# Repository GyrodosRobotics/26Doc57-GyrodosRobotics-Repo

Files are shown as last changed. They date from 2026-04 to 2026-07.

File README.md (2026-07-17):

<p align="center">
  <img src="https://github.com/GyrodosRobotics/26Doc57-GyrodosRobotics-Repo/raw/9fe3f917eb2502e8cde8e8454340d48af9c0934f/docs/gyrodos-fulllogo.png" alt="Gyrodos Robotics Logo" width=300"/>
</p>

<h1 align="center">Gyrodos Robotics</h1>
<h3 align="center">La Salle College, Hong Kong • Est. 2024</h3>

<p align="center">
  <a href="https://sites.google.com/view/gyrodosrobotics">
    
  </a>
  <a href="https://www.instagram.com/gyrodosrobotics">
    
  </a>
  
  
</p>

---

## About

Gyrodos Robotics is a Hong Kong-based underwater robotics team 
from La Salle College, competing in the MATE ROV Competition. 
Formed in 2024, we are composed of 24 members from Year 7 to 
Year 11 devoted to developing innovative solutions to ocean 
preservation challenges and contributing to the UN Sustainable 
Development Goals 13 and 14.

This repository contains the complete technical output of our 
2026 competition season, including mechanical designs, software systems, 
documentation and internal records that are released openly to support 
the underwater robotics community.

---

## Our Vehicles

### ROV Palkia (26Mec34)
Second-generation Gyrodos flagship ROV. CNC-machined 6061T5 
aluminium frame, dual two-axis Dragon Claw grippers, 
8-camera Compound Eye array with stereo vision and YOLOv11 
invasive species detection, fully_vectored8 thruster layout 
with pseudo-inverse mixing matrix, and the LUCARIO software 
stack over RS422.

### Float Magikarp (26Mag42)
Vertical Profiling Float for below-ice environment monitoring. 
500cc syringe buoyancy engine, PID depth control, Bluetooth 
data transmission, and magnetic reed switch power system.
Built in one month alongside Palkia.

---

## Highlighted Systems

### LUCARIO (267X)
**Logistical Underwater Control and Relay Interface Operator**

Our primary software stack for ROV command, control and monitoring.
Split into independent Core and GUI processes communicating over ZMQ,
with RS422 serial connection to the Arduino Mega at 115200 baud.
Features a precomputed 6×8 pseudo-inverse thruster mixing matrix 
for full 6-DOF control, PID autostabilisation, and the False Swipe 
power management system.

→ [View LUCARIO Code](https://github.com/GyrodosRobotics/26Doc57-GyrodosRobotics-Repo/tree/main/Gyrodos%20G2.2/267X-LUCARIO)

### Dragon Claw (263X)
Dual two-axis gripper system with left and right claws using 
different drive modes to imitate arm and wrist movement. 
60kg IP68 waterproof servo and NEMA 17 stepper with worm gear 
adaptor. Compatible with the Grass Grip friction booster.

→ [View CAD Files](https://github.com/GyrodosRobotics/26Doc57-GyrodosRobotics-Repo/tree/main/Gyrodos%20G2.2/223X-Gyrodos%20ROV/26Mec34-Palkia)

### Grass Grip (223X)
Passive biomimetic extension that distributes clamping force across 
hundreds of contact points for improved grip on irregular objects.
Inspired by 3D printed grass and the principles behind SpiRob 
soft robotics research. Clips onto Dragon Claw in 15 seconds 
without tools.

→ [View STL Files](https://github.com/GyrodosRobotics/26Doc57-GyrodosRobotics-Repo/tree/main/Gyrodos%20G2.2/223X-Gyrodos%20ROV/26Mec34-Palkia)

### Crab Detection (261X)
YOLOv11 model trained on 419 annotated images to identify 
invasive European Green Crab against native Rock and Jonah Crab 
species. mAP50 of 97.4%. Includes undistortion pipeline for 
wide-angle AHD cameras.

→ [View Dedicated Repository](https://github.com/GyrodosRobotics/gyrodos-crab-detection)

---

## Competition Results

| Year | Competition | Result |
|---|---|---|
| 2025 | MATE ROV Ranger Hong Kong Regional | 9th |
| 2026 | MATE ROV Ranger Hong Kong Regional | 6th |
| 2026 | MATE ROV Ranger Hong Kong Regional | Best Team Spirit |
| 2026 | MATE ROV Scout Hong Kong Regional | 2nd |

---

## Documentation

All documents submitted to the 2026 MATE ROV Competition 
are available in `265X-Documentation/`:

- **Technical Documentation** — 25-page full system description
- **Company Spec Sheet** — vehicle specifications
- **JSEA** — Job Safety and Environmental Analysis
- **SID** — System Integration Diagrams for ROV and Float
- **Float Magikarp Specs** — vertical profiling float documentation
- **Company Safety Review** — pre-competition safety verification

---

## Open Source Contributions

| Repository | Description |
|---|---|
| [gyrodos-crab-detection](https://github.com/GyrodosRobotics/gyrodos-crab-detection) | YOLOv11 invasive crab detection model and dataset |
| [This repository](https://github.com/GyrodosRobotics/26Doc57-GyrodosRobotics-Repo) | Complete 2026 season mechanical, software and documentation files |

---

## Team

**C-Suite:**
Keanu Lam (CEO) · Gordon Peng (CTO) · Yiming Huang (COO) · 
Jason Lo (CIO) · David Wang (CQO) · Nixon Li (CMO) · 
Mitchell Au (HR) · Henry Lau (Club Chairman)

**Mentors:** Rex · Jimmy · Cloof · Max

**Teacher Advisor:** Mr Terry Lam · Mr Gary Ho · Mr Timothy Goh · Mr Jonathan Sze

**Full team roster:** See Technical Documentation p.4

---

## Acknowledgements

- Leaplight Limited — CNC machining of aluminium frame
- Makerholic Limited — 3D printing services
- Sparks Solutions — Arduino and relay components
- Autodesk Inc. — Fusion 360 Student licence
- La Salle College — laser cutting equipment and pool access
- MATE Center, MATE II and IET Hong Kong — organising the 
  2026 Hong Kong Regional

---

## Licence

Code: [MIT Licence](LICENSE)  
Dataset and model weights: [CC BY 4.0](https://creativecommons.org/licenses/by/4.0/)  
Documentation: All rights reserved, Gyrodos Robotics 2026

---

<p align="center">
  <em>Gyrodos Robotics • La Salle College • Hong Kong • Est. 2024</em>
</p>

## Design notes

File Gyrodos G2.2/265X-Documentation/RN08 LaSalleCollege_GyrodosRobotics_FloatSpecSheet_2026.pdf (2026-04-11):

### EST. 2024 • HKG

# FLOAT MAGIKARP

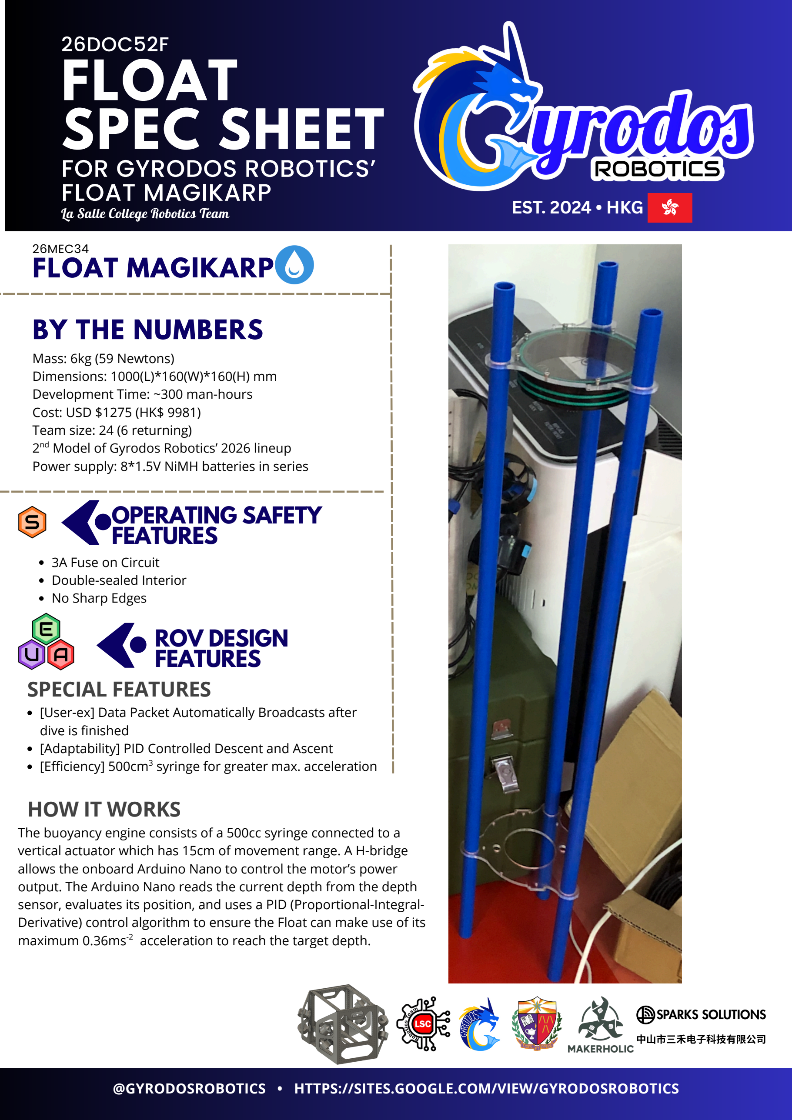
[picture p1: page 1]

SPARKS SOLUTIONS

中山 | 市三⽲电⼦科技有限公司

## ROV DESIGN FEATURES

[User-ex] Data Packet Automatically Broadcasts after dive is finished
[Adaptability] PID Controlled Descent and Ascent [Efficiency] 500cm syringe for greater max. acceleration

3

3A Fuse on Circuit
Double-sealed Interior
No Sharp Edges

The buoyancy engine consists of a 500cc syringe connected to a vertical actuator which has 15cm of movement range. A H-bridge allows the onboard Arduino Nano to control the motor’s power output. The Arduino Nano reads the current depth from the depth sensor, evaluates its position, and uses a PID (Proportional-Integral-Derivative) control algorithm to ensure the Float can make use of its maximum 0.36ms acceleration to reach the target depth.

-2

@GYRODOSROBOTICS • HTTPS://SITES.GOOGLE.COM/VIEW/GYRODOSROBOTICS

# FLOAT SPEC SHEET

# FOR GYRODOS ROBOTICS’ FLOAT MAGIKARP

## SPECIAL FEATURES

## OPERATING SAFETY FEATURES

## HOW IT WORKS

## 26DOC52F

# BY THE NUMBERS

Mass: 6kg (59 Newtons)
Dimensions: 1000(L)*160(W)*160(H) mm Development Time: ~300 man-hours Cost: USD $1275 (HK$ 9981)
Team size: 24 (6 returning)
2 Model of Gyrodos Robotics’ 2026 lineup

nd
Power supply: 8*1.5V NiMH batteries in series

26MEC34

La Salle College Robotics Team

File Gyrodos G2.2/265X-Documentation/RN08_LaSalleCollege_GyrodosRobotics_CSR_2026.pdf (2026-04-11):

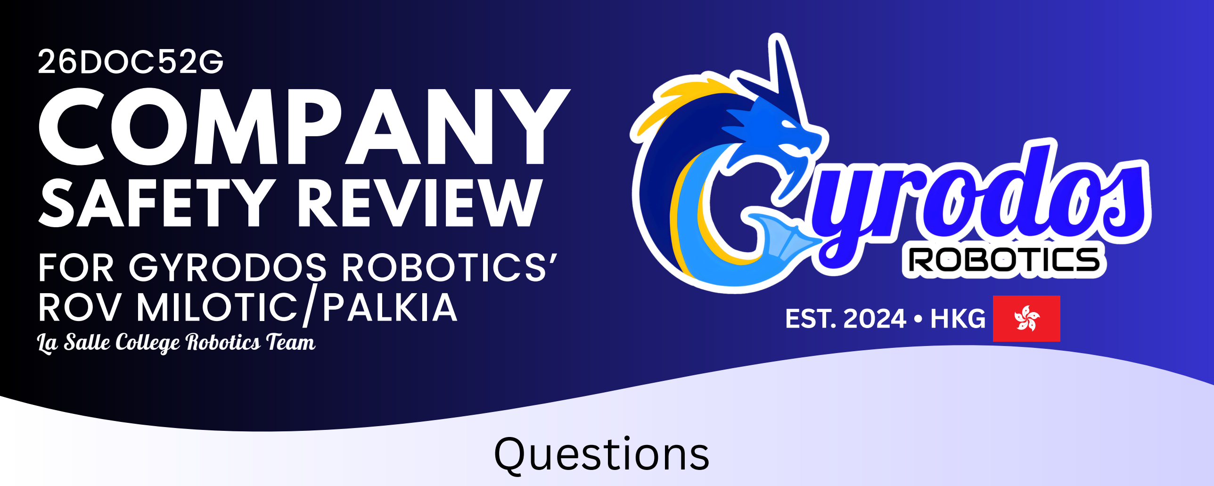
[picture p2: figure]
JSEA BY; EST. 2024 • HKG; COMPANY SAFETY REVIEW FOR GYRODOS ROBOTICS’ ROV MILOTIC/PALKIA; La Salle College Robotics Team; 26DOC52G; Questions

1.The main point of connection is via Anderson Powerpole Connectors.
2.The Fuse is 12cm away from the Anderson Powerpole Connector and was measured with a ruler.
3.The FLA was 22.4A, and a 25A Fuse was used.
4. The maximum current of the Thruster Block is 18A. Max current of Claw Block is 3.36A. The maximum current of the sensors is 1A.
5.All wires have proper Strain Relief.
6.There is no exposed wiring.
7.The wires are neatly laid out in the Control Box. 8.There is one AC wire, which supplies the 230V AC to 12V DC Converter.
9.There is one Macbook as the onshore processor. Some external displays act as secondary displays for the system.
10.The controller (and joystick) used is the Nintendo Switch Pro Controller.

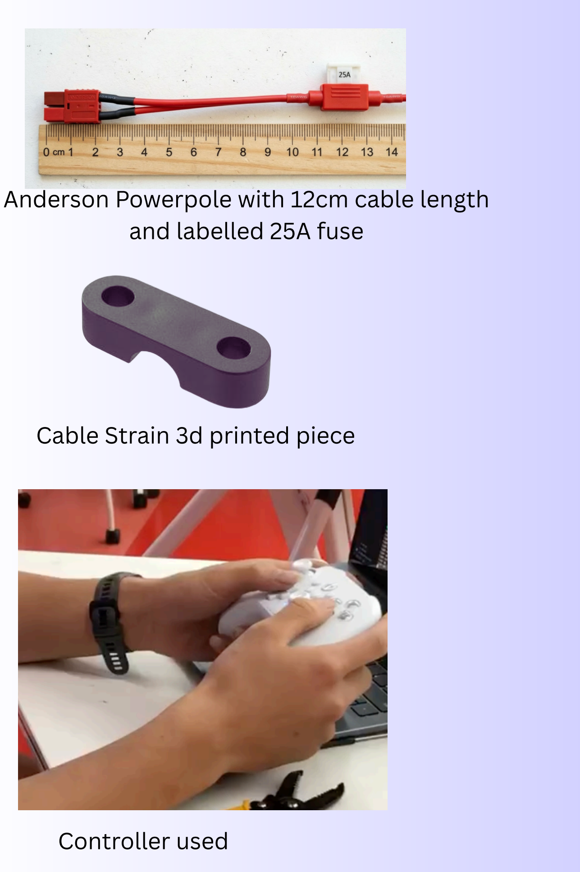
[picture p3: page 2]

Anderson Powerpole with 12cm cable length and labelled 25A fuse

Cable Strain 3d printed piece

Controller used

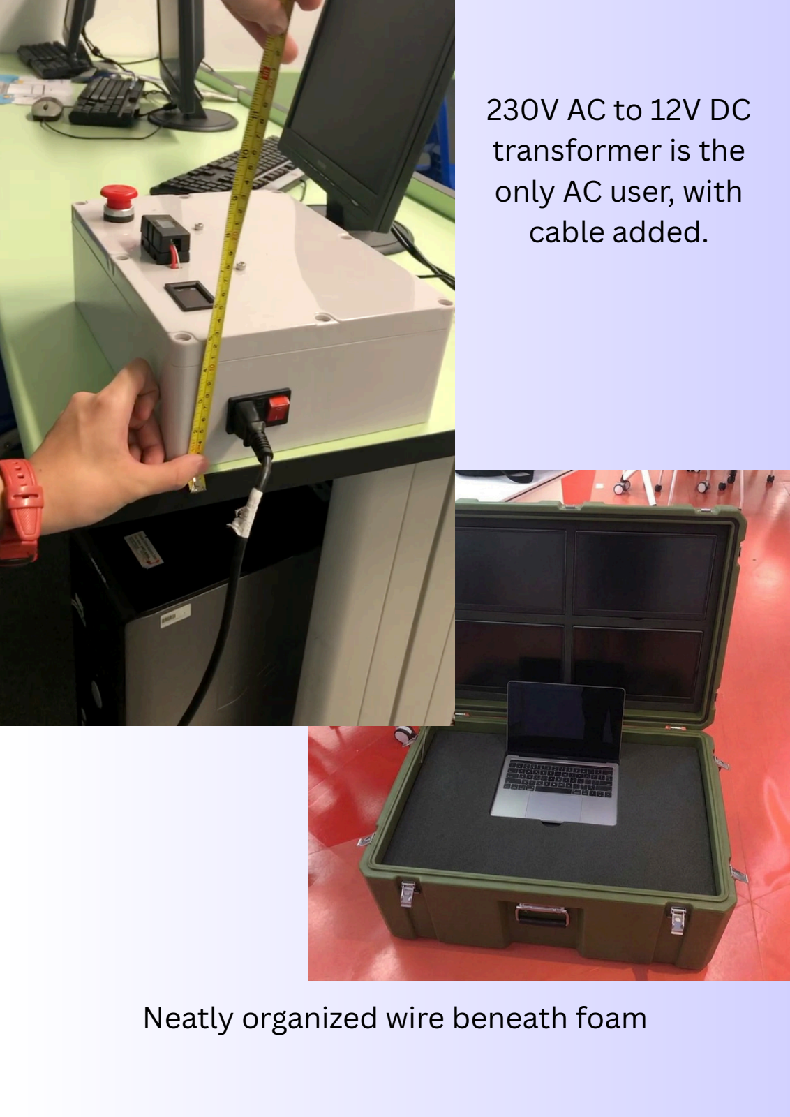
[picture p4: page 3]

Neatly organized wire beneath foam

230V AC to 12V DC
transformer is the
only AC user, with
cable added.

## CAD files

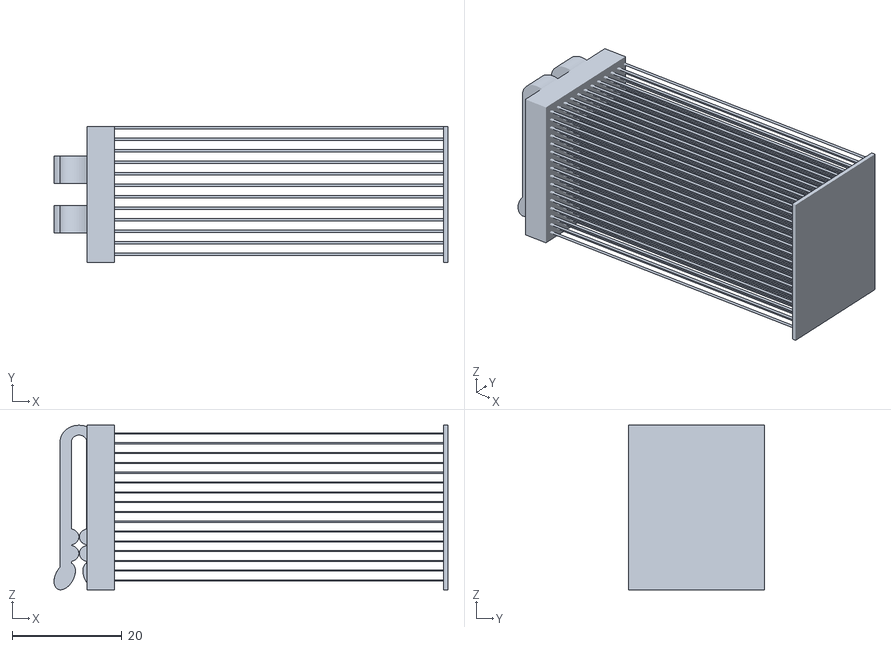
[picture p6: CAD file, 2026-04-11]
Gyrodos G2.2/223X-Gyrodos ROV/26Mec34-Palkia/Grass Grip (1).stl
71.8 x 24.7 x 30.0

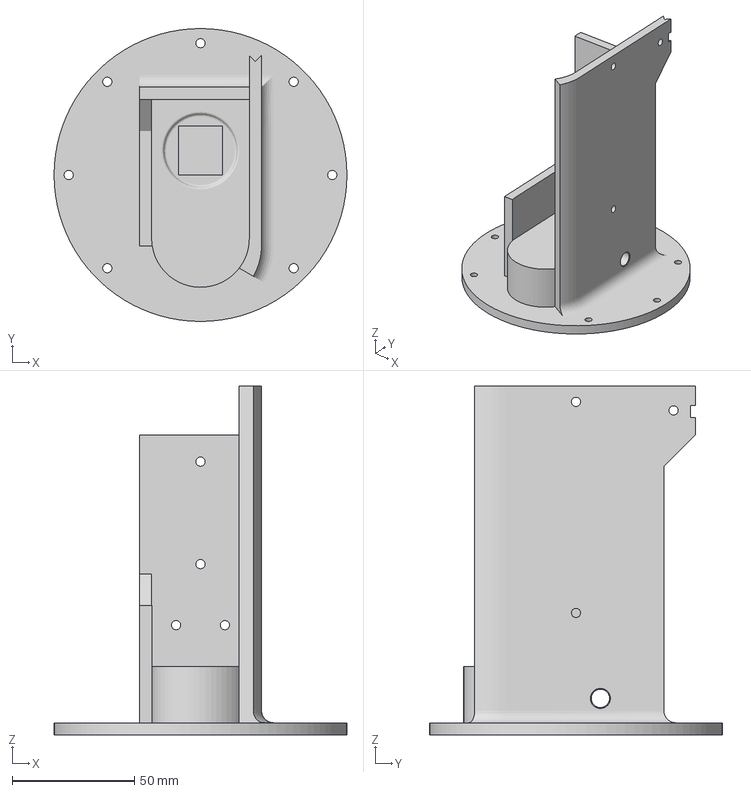
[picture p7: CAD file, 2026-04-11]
Gyrodos G2.2/264X-Magikarp Float/26Mag42-Float Magikarp/Magikarp PAWMO.3mf
120.0 x 120.0 x 143.0 mm

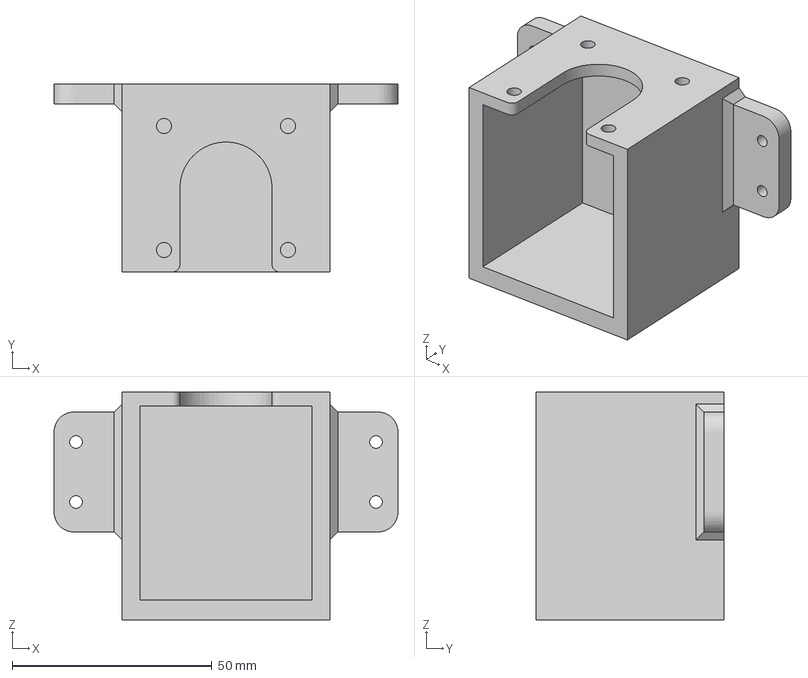
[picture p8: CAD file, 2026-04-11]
Gyrodos G2.2/223X-Gyrodos ROV/26Mec34-Palkia/Palkia- Stepper Holder R.3mf
86.0 x 47.0 x 57.0 mm

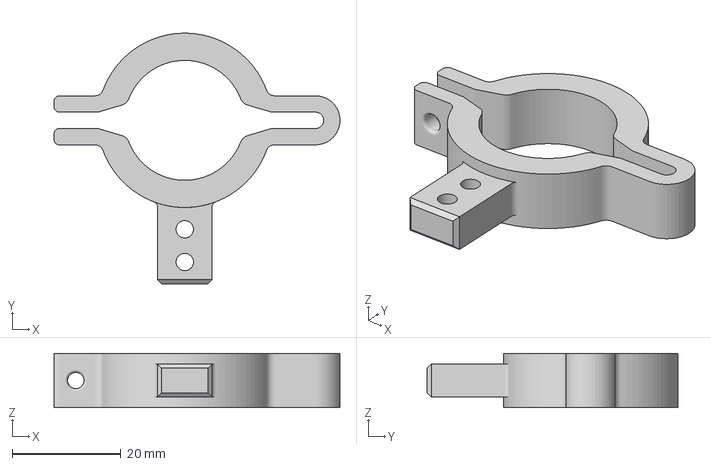
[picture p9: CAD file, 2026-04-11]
Gyrodos G2.2/223X-Gyrodos ROV/26Mec34-Palkia/camera clip top.3mf
52.5 x 46.0 x 10.0 mm

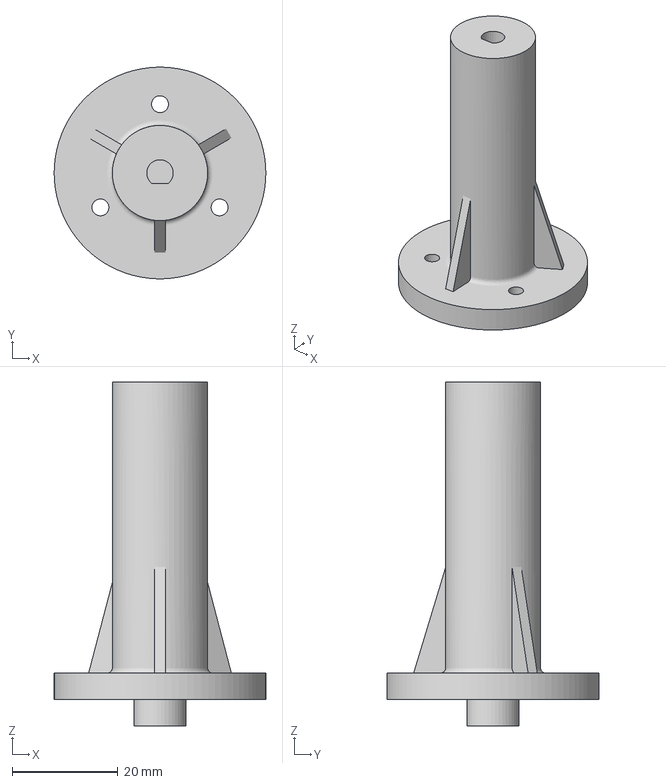
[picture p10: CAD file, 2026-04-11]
Gyrodos G2.2/223X-Gyrodos ROV/26Mec34-Palkia/Palkia - Claw Extension 60.3mf
40.0 x 40.0 x 65.0 mm

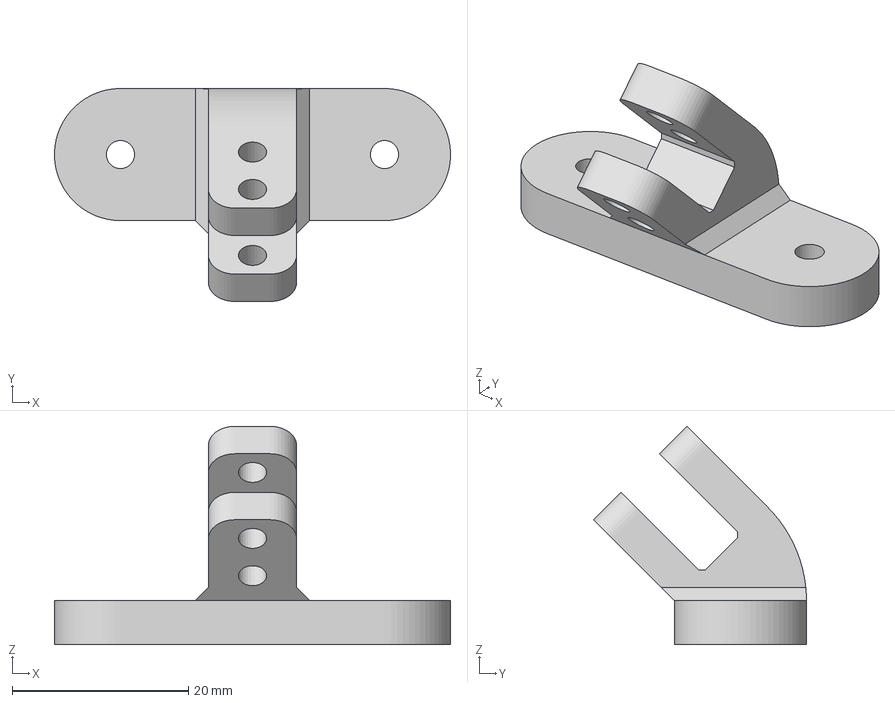
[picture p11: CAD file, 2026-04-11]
Gyrodos G2.2/223X-Gyrodos ROV/26Mec34-Palkia/camera clip bottom 180-45.3mf
45.0 x 24.2 x 24.8 mm

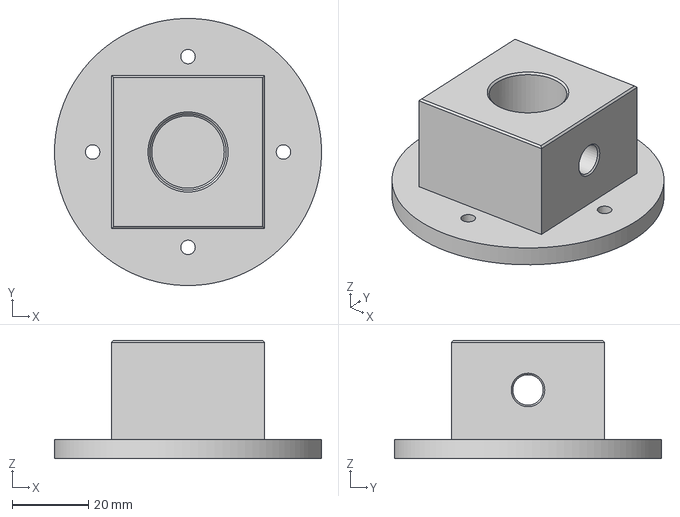
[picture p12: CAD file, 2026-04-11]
Gyrodos G2.2/264X-Magikarp Float/26Mag42-Float Magikarp/Magikarp-Piston adaptor Bottom-Expanded.3mf
70.0 x 70.0 x 31.0 mm

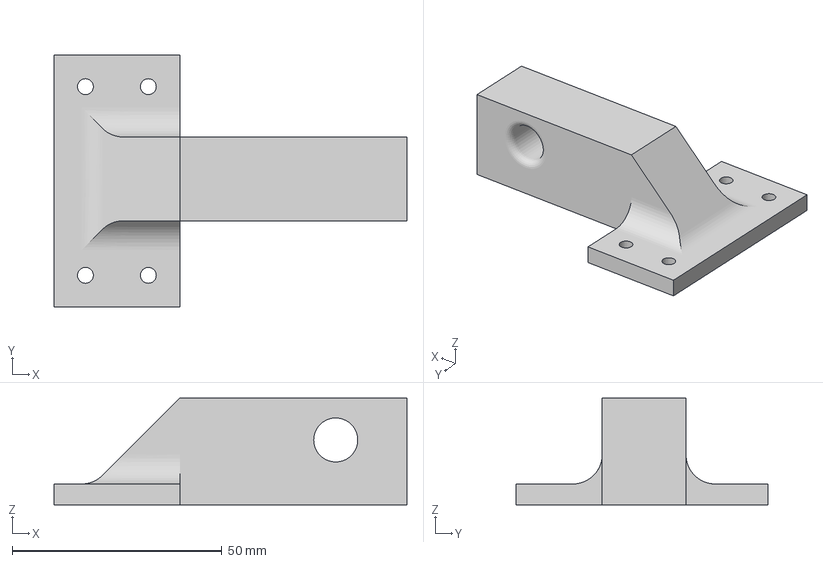
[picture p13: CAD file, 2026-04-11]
Gyrodos G2.2/223X-Gyrodos ROV/26Mec34-Palkia/Palkia-Stepper end loop-expanded.3mf
84.2 x 60.0 x 25.5 mm

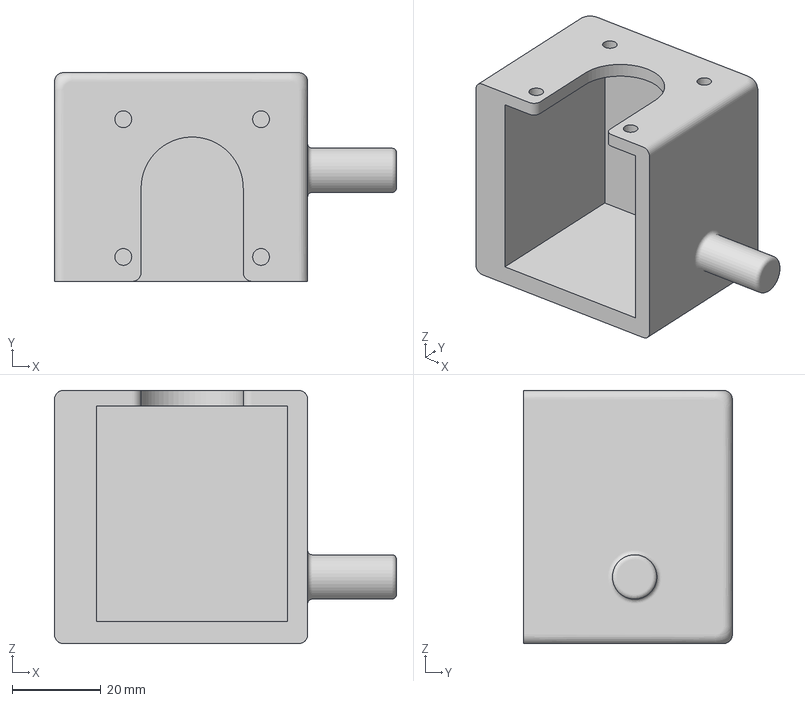
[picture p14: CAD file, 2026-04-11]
Gyrodos G2.2/223X-Gyrodos ROV/26Mec34-Palkia/stepper holder-485f.3mf
77.0 x 47.0 x 57.0 mm

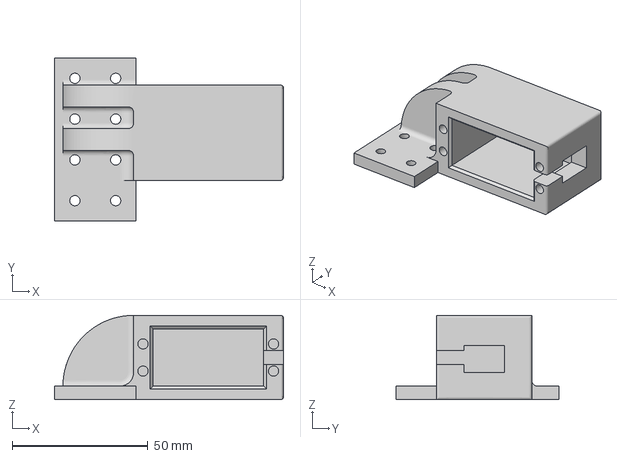
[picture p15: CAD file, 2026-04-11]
Gyrodos G2.2/223X-Gyrodos ROV/26Mec34-Palkia/Palkia- Servo Holder-expanded.3mf
84.2 x 60.0 x 31.0 mm

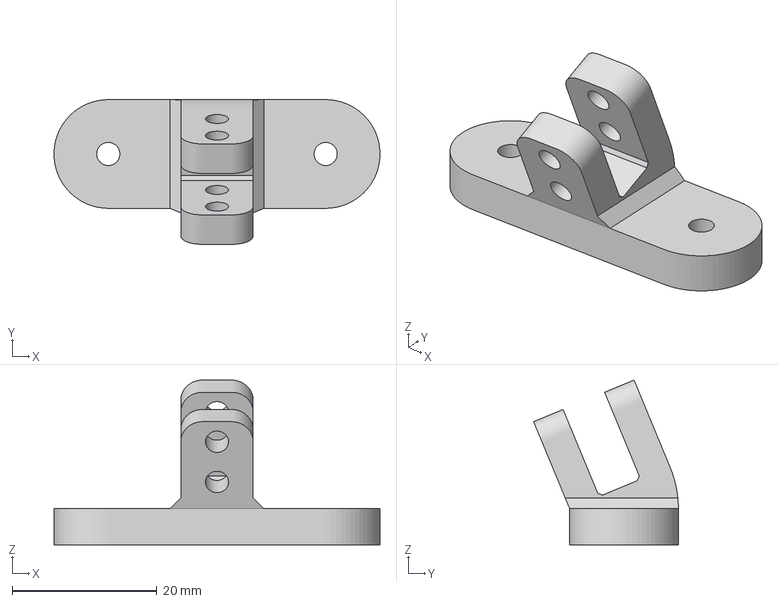
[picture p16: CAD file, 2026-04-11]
Gyrodos G2.2/223X-Gyrodos ROV/26Mec34-Palkia/camera clip bottom 180-675.3mf
45.0 x 20.0 x 22.8 mm

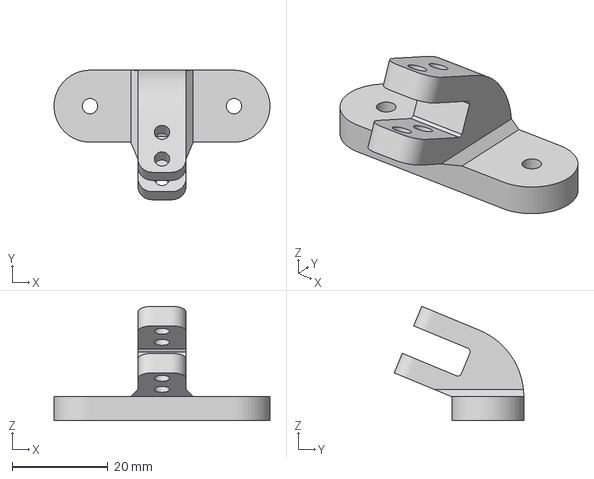
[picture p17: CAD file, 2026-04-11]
Gyrodos G2.2/223X-Gyrodos ROV/26Mec34-Palkia/camera clip bottom 180-225.3mf
45.0 x 27.0 x 23.8 mm

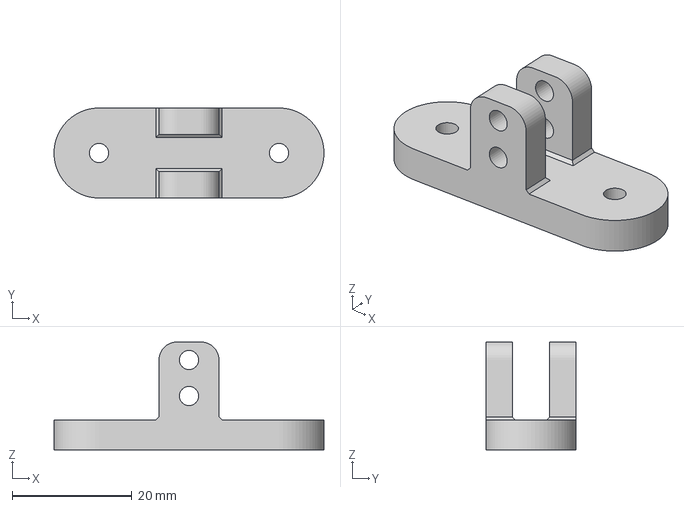
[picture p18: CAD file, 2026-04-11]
Gyrodos G2.2/223X-Gyrodos ROV/26Mec34-Palkia/camera clip bottom 180-90.3mf
45.0 x 15.0 x 18.0 mm

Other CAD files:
Gyrodos G2.2/264X-Magikarp Float/26Mag42-Float Magikarp/endplate-18-18-8-71-ext16-y.dwg
Gyrodos G2.2/264X-Magikarp Float/26Mag42-Float Magikarp/endplate-10-13-8-25-ext175-x.dwg
Gyrodos G2.2/264X-Magikarp Float/26Mag42-Float Magikarp/endplate-0-0-8-0-ext16-x.dwg
Gyrodos G2.2/264X-Magikarp Float/26Mag42-Float Magikarp/endplate-10-10-8-71-ext16-y.dwg

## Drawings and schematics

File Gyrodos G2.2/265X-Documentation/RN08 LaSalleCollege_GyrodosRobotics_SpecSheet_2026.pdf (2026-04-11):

### EST. 2024 • HKG

# ROV PALKIA

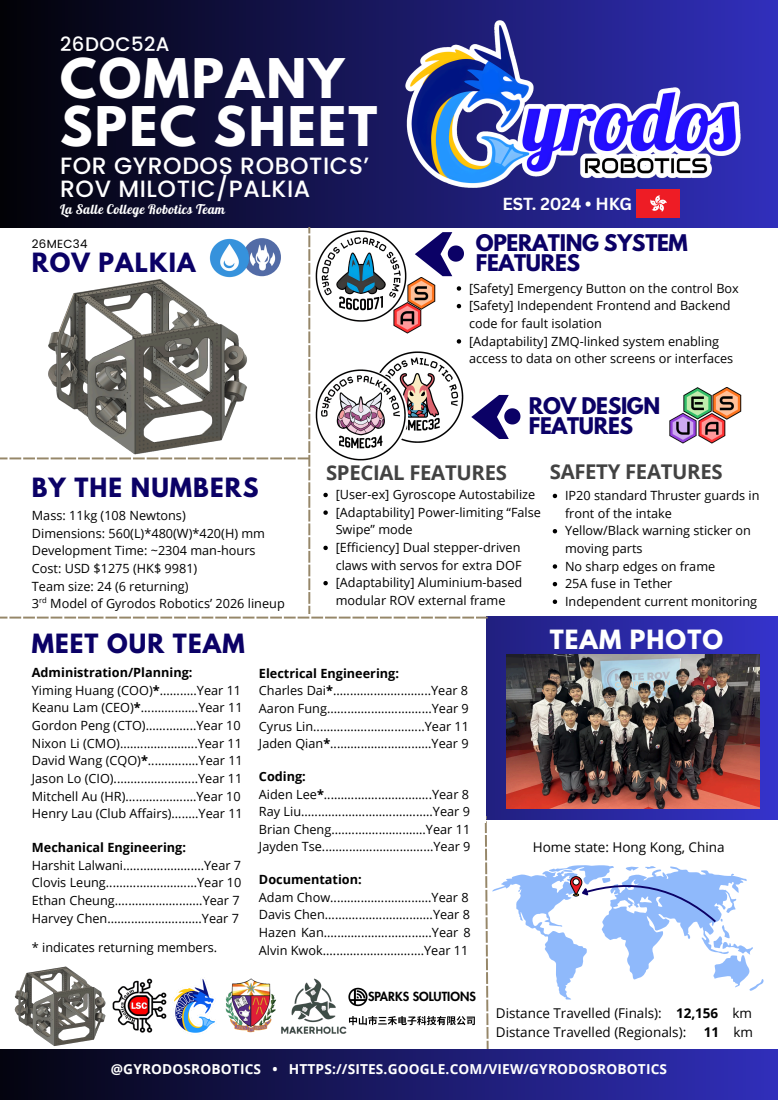
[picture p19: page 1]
SPARKS SOLUTIONS; 市三⽲电⼦科技有限公司; ...........Year 11 .................Year 11; ...............Year 11; .............................Year 8; ..............................Year 9; ................................Year 8; 26MEC34

26DOC52A
COMPANY
SPEC SHEET
FOR GYRODOS ROBOTICS’
ROV MILOTIC/PALKIA
La Salle College Robotics Team

OPERATING SYSTEM
FEATURES
[Safety] Emergency Button on the control Box
[Safety] Independent Frontend and Backend
code for fault isolation
[Adaptability] ZMQ-linked system enabling
access to data on other screens or interfaces
ROV DESIGN
SAFETY FEATURES
IP20 standard Thruster guards in
front of the intake
Yellow/Black warning sticker on
moving parts
No sharp edges on frame
25A fuse in Tether
Independent current monitoring
TEAM PHOTO

SPECIAL FEATURES
[User-ex] Gyroscope Autostabilize
[Adaptability] Power-limiting “False
Swipe” mode
[Efficiency] Dual stepper-driven
claws with servos for extra DOF
[Adaptability] Aluminium-based
modular ROV external frame

BY THE NUMBERS
Mass: 11kg (108 Newtons)
Dimensions: 560(L)*480(W)*420(H) mm
Development Time: ~2304 man-hours
Cost: USD $1275 (HK$ 9981)
Team size: 24 (6 returning)
3 Model of Gyrodos Robotics’ 2026 lineup
MEET OUR TEAM
Administration/Planning:
Yiming Huang (COO)*
Keanu Lam (CEO)*
Gordon Peng (CTO)...............Year 10
Nixon Li (CMO).......................Year 11
David Wang (CQO)*
Jason Lo (CIO).........................Year 11
Mitchell Au (HR).....................Year 10
Henry Lau (Club Affairs)........Year 11

Electrical Engineering:
Charles Dai*
Aaron Fung...............................Year 9
Cyrus Lin.................................Year 11
Jaden Qian*
Coding:
Aiden Lee*
Ray Liu.......................................Year 9
Brian Cheng............................Year 11
Jayden Tse.................................Year 9
Documentation:
Adam Chow..............................Year 8
Davis Chen................................Year 8
Hazen Kan................................Year 8
Alvin Kwok..............................Year 11

Mechanical Engineering:
Harshit Lalwani........................Year 7
Clovis Leung...........................Year 10
Ethan Cheung..........................Year 7
Harvey Chen............................Year 7
* indicates returning members.

Home state: Hong Kong, China

Distance Travelled (Finals): 12,156 km
Distance Travelled (Regionals): 11 km

@GYRODOSROBOTICS • HTTPS://SITES.GOOGLE.COM/VIEW/GYRODOSROBOTICS

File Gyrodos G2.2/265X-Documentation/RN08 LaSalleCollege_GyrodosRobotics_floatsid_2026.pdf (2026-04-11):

# 26DOC52E SYSTEM

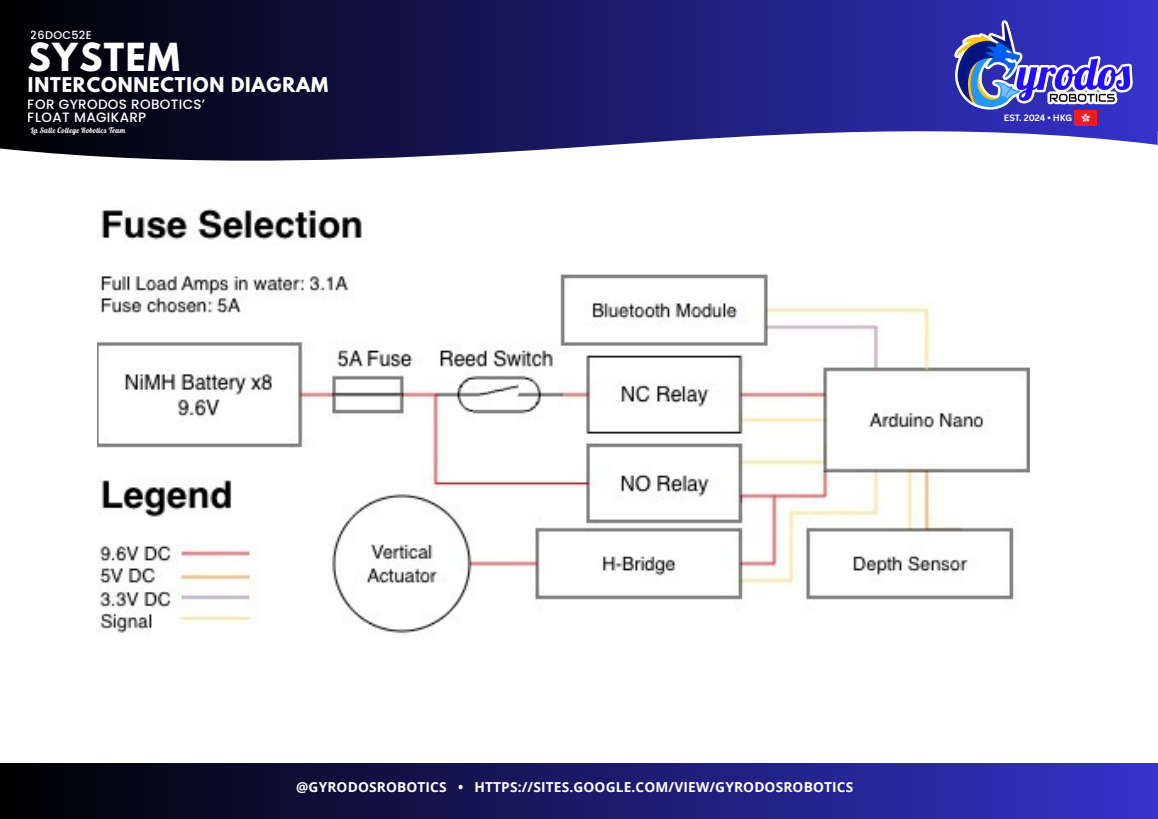
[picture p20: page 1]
EST. 2024 • HKG

INTERCONNECTION DIAGRAM
FOR GYRODOS ROBOTICS’
FLOAT MAGIKARP

La Salle College Robotics Team

@GYRODOSROBOTICS • HTTPS://SITES.GOOGLE.COM/VIEW/GYRODOSROBOTICS

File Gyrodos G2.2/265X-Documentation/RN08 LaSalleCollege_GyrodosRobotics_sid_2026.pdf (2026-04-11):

# 26DOC52E SYSTEM

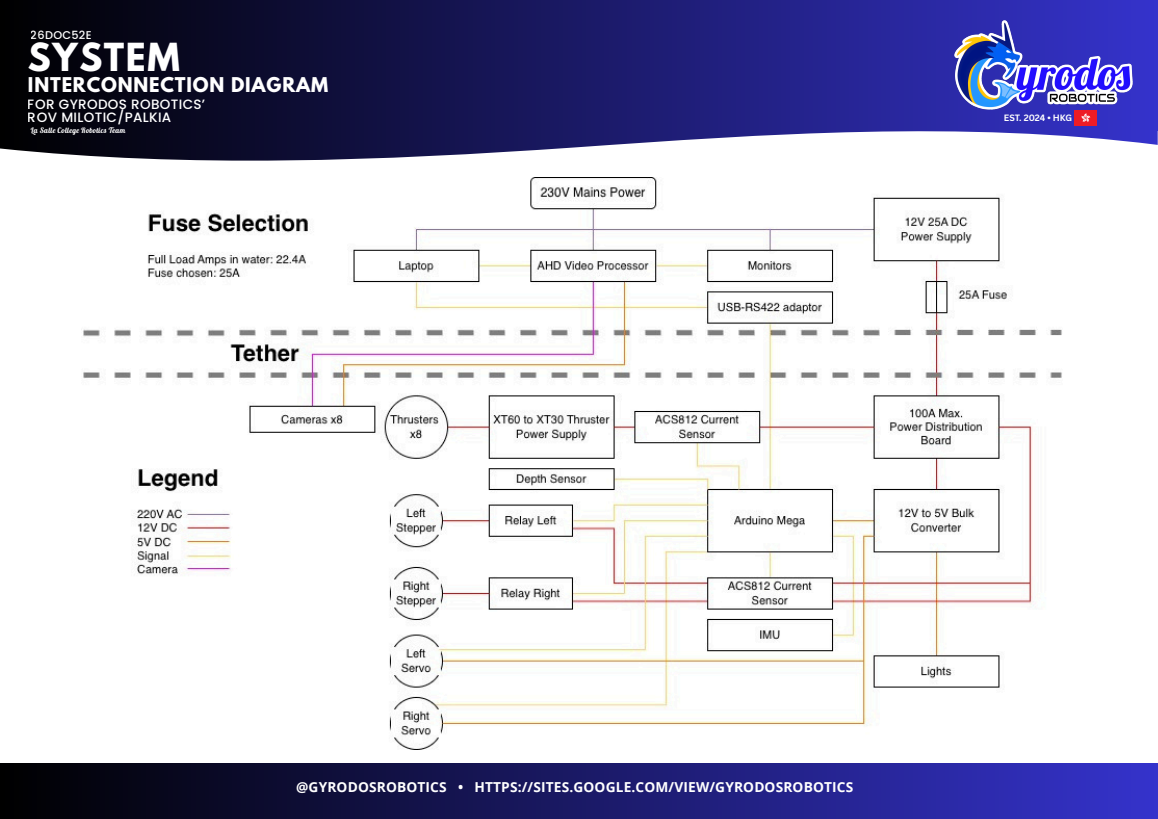
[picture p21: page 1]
EST. 2024 • HKG

INTERCONNECTION DIAGRAM
FOR GYRODOS ROBOTICS’
ROV MILOTIC/PALKIA

La Salle College Robotics Team

@GYRODOSROBOTICS • HTTPS://SITES.GOOGLE.COM/VIEW/GYRODOSROBOTICS

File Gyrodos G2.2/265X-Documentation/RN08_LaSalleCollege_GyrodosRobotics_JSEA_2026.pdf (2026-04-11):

# JSEA BY

# EST. 2024 • HKG

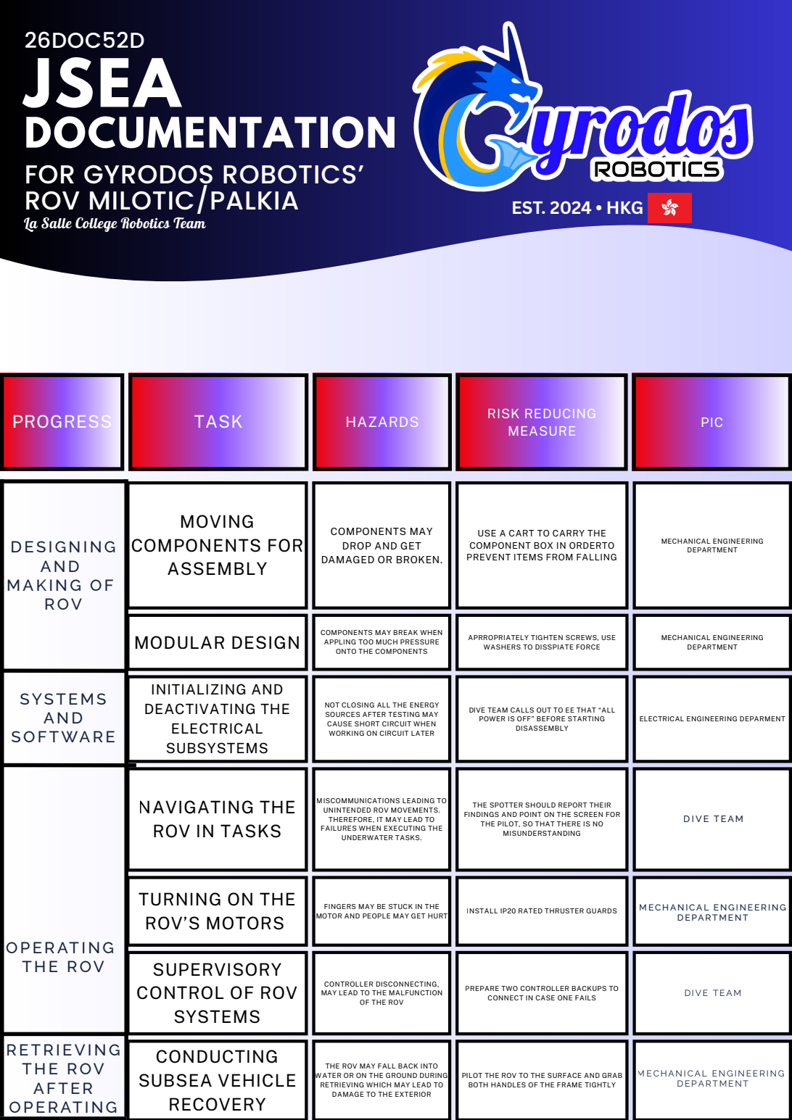
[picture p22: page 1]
PROGRESS; TASK; HAZARDS; RISK REDUCING MEASURE; PIC; MOVING COMPONENTS FOR ASSEMBLY; MECHANICAL ENGINEERING DEPARTMENT; MODULAR DESIGN; INITIALIZING AND DEACTIVATING THE ELECTRICAL SUBSYSTEMS; DISASSEMBLY; INSTALL IP20 RATED THRUSTER GUARDS; CONDUCTING SUBSEA VEHICLE RECOVERY; D ESI GNING AND M AKING O F R OV; SYSTE M S AND S O FTWARE; O PERATING T H E R OV; RETRIEVING T H E R OV AFTER O PERATING; D EPART M ENT; D IVE TEA M

26DOC52D
JSEA
DOCUMENTATION
FOR GYRODOS ROBOTICS’
ROV MILOTIC/PALKIA
La Salle College Robotics Team

COMPONENTS MAY
DROP AND GET
DAMAGED OR BROKEN.

USE A CART TO CARRY THE
COMPONENT BOX IN ORDERTO
PREVENT ITEMS FROM FALLING

COMPONENTS MAY BREAK WHEN
APPLING TOO MUCH PRESSURE
ONTO THE COMPONENTS

APRROPRIATELY TIGHTEN SCREWS, USE
WASHERS TO DISSPIATE FORCE

NOT CLOSING ALL THE ENERGY
SOURCES AFTER TESTING MAY
CAUSE SHORT CIRCUIT WHEN
WORKING ON CIRCUIT LATER

DIVE TEAM CALLS OUT TO EE THAT “ALL
POWER IS OFF” BEFORE STARTING

ELECTRICAL ENGINEERING DEPARMENT

NAVIGATING THE
ROV IN TASKS

MISCOMMUNICATIONS LEADING TO
UNINTENDED ROV MOVEMENTS.
THEREFORE, IT MAY LEAD TO
FAILURES WHEN EXECUTING THE
UNDERWATER TASKS.

THE SPOTTER SHOULD REPORT THEIR
FINDINGS AND POINT ON THE SCREEN FOR
THE PILOT, SO THAT THERE IS NO
MISUNDERSTANDING

TURNING ON THE
ROV’S MOTORS

FINGERS MAY BE STUCK IN THE
MOTOR AND PEOPLE MAY GET HURT

M EC H ANICAL ENG INEERING

SUPERVISORY
CONTROL OF ROV
SYSTEMS

CONTROLLER DISCONNECTING,
MAY LEAD TO THE MALFUNCTION

PREPARE TWO CONTROLLER BACKUPS TO
CONNECT IN CASE ONE FAILS

OF THE ROV

THE ROV MAY FALL BACK INTO
WATER OR ON THE GROUND DURING
RETRIEVING WHICH MAY LEAD TO
DAMAGE TO THE EXTERIOR

PILOT THE ROV TO THE SURFACE AND GRAB
BOTH HANDLES OF THE FRAME TIGHTLY

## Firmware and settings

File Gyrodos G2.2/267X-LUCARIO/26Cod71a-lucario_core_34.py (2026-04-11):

#!/usr/bin/env python3
"""
26Cod71a
LUCARIO Core [ver 34] v2.2 — headless ROV control backend

Manages:
  • Serial communication with Arduino Mega over RS422
  • Nintendo Switch Pro Controller input via pygame
  • 6-DOF thruster allocation via precomputed mixing matrix
  • Camera feeds over ZMQ
  • State publishing and command handling over ZMQ
  • Power management override relay (v2.2)

Gyrodos Robotics

TO solve 5556 in use issue:
lsof -i:5556
kill -9 <PID>
"""

import os
import sys
import zmq
import json
import time
import struct
import threading
import math
import argparse
import numpy as np
from dataclasses import dataclass, field, asdict
from typing import List, Optional

try:
    import cv2
    HAS_CV2 = True
except ImportError:
    HAS_CV2 = False

try:
    import serial as pyserial
    HAS_SERIAL = True
except ImportError:
    HAS_SERIAL = False

try:
    import pygame
    HAS_PYGAME = True
except ImportError:
    HAS_PYGAME = False


# ═══════════════════════════════════════════════════════════════
#  ROV STATE (single source of truth)
# ═══════════════════════════════════════════════════════════════
@dataclass
class ROVState:
    # Attitude & navigation
    pitch: float = 0.0              # degrees (from accel, positive = nose up)
    roll: float = 0.0               # degrees (from accel, positive = right down)
    heading: float = 0.0            # degrees (requires magnetometer — placeholder)
    depth: float = 0.0              # metres

    # Derived motion (placeholder — integrate later)
    speed: float = 0.0
    vert_speed: float = 0.0

    # Environment
    temperature: float = 0.0        # °C
    pressure: float = 0.0           # mbar
    amperage: float = 0.0           # A

    # Thrusters — display values in -100..+100  (0 = neutral)
    thruster_val: List[int] = field(default_factory=lambda: [0] * 8)
    thruster_powered: List[bool] = field(default_factory=lambda: [True] * 8)
    thruster_inverted: List[bool] = field(default_factory=lambda: [False] * 8)
    thruster_inop: List[bool] = field(default_factory=lambda: [False] * 8)
    thruster_trim: List[float] = field(default_factory=lambda: [0.0] * 8)

    # Manipulators
    left_stepper_deg: float = 0.0
    right_stepper_deg: float = 0.0
    left_servo_deg: float = 90.0
    right_servo_deg: float = 90.0

    # Raw IMU
    accel_x: float = 0.0           # g
    accel_y: float = 0.0           # g
    accel_z: float = 0.0           # g
    gyro_x: float = 0.0            # °/s
    gyro_y: float = 0.0            # °/s
    gyro_z: float = 0.0            # °/s

    # Tool / measurement
    distance: float = 0.0
    measuring: bool = False

    # Modes & flags
    autostab: bool = False
    false_swipe: bool = False
    lights: bool = False
    emergency: bool = False
    right_claw_open: bool = False
    left_claw_open: bool = False
    serial_connected: bool = False
    controller_connected: bool = False

    # Power management (v2.2 — from Arduino v1.2 telemetry)
    throttle_percent: int = 0       # 0–100, auto-throttle on thrusters
    shutdown_bitmask: int = 0       # 8-bit module shutdown status
    override_mode: int = 0x88       # 0x00=forbid, 0x88=auto, 0xFF=manual cut
    controls_locked: bool = False   # v2.2 — lock controller input from GUI



# ═══════════════════════════════════════════════════════════════
#  THRUSTER MIXING MATRIX
# ═══════════════════════════════════════════════════════════════
class ThrusterController:
    """
    6-DOF wrench (fx, fy, fz, tx, ty, tz) → 8 thruster powers
    via precomputed pseudo-inverse of the geometry matrix.
    """

    def __init__(self):
        positions = np.array([
            [ 24,  16,  8], [ 24, -16,  8],
            [-24,  16,  8], [-24, -16,  8],
            [ 24,  16, -8], [ 24, -16, -8],
            [-24,  16, -8], [-24, -16, -8],
        ], dtype=np.float32)

        directions = np.array([
            [ 1, -1, -1], [ 1,  1, -1],
            [-1, -1, -1], [-1,  1, -1],
            [ 1, -1,  1], [ 1,  1,  1],
            [-1, -1,  1], [-1,  1,  1],
        ], dtype=np.float32)
        directions /= np.linalg.norm(directions[0])  # normalise

        # Build 6×8 mixing matrix  [forces; torques] = M · thrusters
        M = np.zeros((6, 8), dtype=np.float32)
        for i in range(8):
            r, f = positions[i], directions[i]
            M[:3, i] = f                                    # force
            M[3, i] = r[1] * f[2] - r[2] * f[1]            # roll  torque
            M[4, i] = r[2] * f[0] - r[0] * f[2]            # pitch torque
            M[5, i] = r[0] * f[1] - r[1] * f[0]            # yaw   torque

        self._M_inv = np.linalg.pinv(M).astype(np.float32)  # 8×6

    def allocate(self, fx: float, fy: float, fz: float,
                 tx: float, ty: float, tz: float) -> np.ndarray:
        """Returns 8 thruster powers in [-1.0, +1.0]."""
        wrench = np.array([fx, fy, fz, tx, ty, tz], dtype=np.float32)
        powers = self._M_inv @ wrench

        peak = np.abs(powers).max()
        if peak < 1e-6:
            return np.zeros(8, dtype=np.float32)

        powers /= peak

        command_mag = min(float(np.abs(wrench).max()), 1.0)
        powers *= command_mag

        return powers


# ═══════════════════════════════════════════════════════════════
#  COMPLEMENTARY FILTER — fuse accel + gyro for stable attitude
# ═══════════════════════════════════════════════════════════════
class ComplementaryFilter:
    """
    Blends gyroscope (fast, drifts) with accelerometer (slow, noisy).

    alpha close to 1.0 → trust gyro more (smooth, but drifts over time)
    alpha close to 0.0 → trust accel more (noisy, but no drift)

    0.96–0.98 is typical for 50 Hz update with moderate vibration.
    """

    def __init__(self, alpha: float = 0.97):
        self.alpha = alpha
        self.pitch = 0.0
        self.roll = 0.0
        self._initialized = False

    def update(self, accel_pitch: float, accel_roll: float,
               gyro_x: float, gyro_y: float, dt: float):
        if not self._initialized:
            self.pitch = accel_pitch
            self.roll = accel_roll
            self._initialized = True
            return

        self.pitch = self.alpha * (self.pitch + gyro_y * dt) \
                     + (1 - self.alpha) * accel_pitch
        self.roll = self.alpha * (self.roll + gyro_x * dt) \
                    + (1 - self.alpha) * accel_roll


# ═══════════════════════════════════════════════════════════════
#  PID CONTROLLER
# ═══════════════════════════════════════════════════════════════
class PIDController:

    def __init__(self, kp: float, ki: float, kd: float,
                 integral_limit: float = 0.3,
                 output_limit: float = 0.4,
                 derivative_filter: float = 0.7):
        self.kp = kp
        self.ki = ki
        self.kd = kd
        self.integral_limit = integral_limit
        self.output_limit = output_limit
        self.d_filter = derivative_filter

        self._integral = 0.0
        self._prev_error = 0.0
        self._prev_derivative = 0.0
        self._initialized = False

    def update(self, target: float, measured: float, dt: float) -> float:
        error = target - measured

        p = self.kp * error

        self._integral += error * dt
        self._integral = max(-self.integral_limit,
                             min(self.integral_limit, self._integral))
        i = self.ki * self._integral

        if not self._initialized:
            raw_d = 0.0
            self._initialized = True
        else:
            raw_d = (error - self._prev_error) / dt

        filtered_d = (self.d_filter * self._prev_derivative
                      + (1 - self.d_filter) * raw_d)
        self._prev_derivative = filtered_d
        d = self.kd * filtered_d

        self._prev_error = error

        output = p + i + d
        return max(-self.output_limit, min(self.output_limit, output))

    def reset(self):
        self._integral = 0.0
        self._prev_error = 0.0
        self._prev_derivative = 0.0
        self._initialized = False

# ═══════════════════════════════════════════════════════════════
#  SERIAL INTERFACE — RS422  ↔  Arduino Mega
# ═══════════════════════════════════════════════════════════════
#
#  Packet wire format (both directions):
#    [0xAA] [CMD] [LEN] [PAYLOAD × LEN] [CHECKSUM]
#    checksum = (sum of all preceding bytes) & 0xFF
#
#  TX  CMD 0x01  Thruster   LEN=8   payload: 8 × uint8  (0–200, 100=stop)
#  TX  CMD 0x02  Actuator   LEN=8   payload: see spec
#    [7] override  0x00=forbid shutdown, 0x88=auto, 0xFF=manual cut
#  RX  CMD 0x03  Telemetry  LEN=20  payload:
#    [0-13]  6 × int16 + 1 × uint16  (LE) — IMU + depth
#    [14]    throttle_percent  uint8  0–100
#    [15]    shutdown_bitmask  uint8  (bit per module)
#    [16-17] temperature       int16  centi-°C
#    [18-19] amperage          uint16 milli-A
#
# ═══════════════════════════════════════════════════════════════

class SerialInterface:

    START   = 0xAA
    CMD_THR = 0x01
    CMD_ACT = 0x02
    CMD_TEL = 0x03

    # parser states
    S_START, S_CMD, S_LEN, S_DATA, S_CS = range(5)

    def __init__(self, state: ROVState,
                 port: str = '/dev/ttyUSB0', baud: int = 115200):
        self.st = state
        self._port = port
        self._baud = baud
        self._ser: Optional[pyserial.Serial] = None
        self._lock = threading.Lock()       # guards _ser.write()
        self._running = False
        self._thread: Optional[threading.Thread] = None
        self._last_rx: float = 0.0          # monotonic timestamp
        # parser scratch
        self._ps   = self.S_START
        self._cmd  = 0
        self._dlen = 0
        self._buf  = bytearray()
        self._idx  = 0
        self._csum = 0


    # ── lifecycle ──

    def connect(self) -> bool:
        if not HAS_SERIAL:
            print("[SERIAL] pyserial not installed — running without hardware")
            return False
        try:
            self._ser = pyserial.Serial(self._port, self._baud, timeout=0.01)
            time.sleep(0.1)
            self._running = True
            self._thread = threading.Thread(target=self._rx_loop, daemon=True)
            self._thread.start()
            self.st.serial_connected = True
            print(f"[SERIAL] Opened {self._port} @ {self._baud}")
            return True
        except Exception as e:
            print(f"[SERIAL] Connect failed: {e}")
            return False

    def disconnect(self):
        self._running = False
        if self._thread:
            self._thread.join(timeout=2)
        if self._ser and self._ser.is_open:
            self._ser.close()
        self.st.serial_connected = False
        print("[SERIAL] Closed")

    # ── transmit helpers ──

    def _packet(self, cmd: int, payload: bytes) -> bytes:
        hdr = bytes([self.START, cmd, len(payload)])
        cs = (sum(hdr) + sum(payload)) & 0xFF
        return hdr + payload + bytes([cs])

    def send_thruster(self, values: List[int]):
        """Send CMD 0x01.  values: list of 8 ints, 0–200, 100 = neutral."""
        if not self._ser or not self._ser.is_open:
            return
        data = bytes(max(0, min(200, v)) for v in values)
        with self._lock:
            self._ser.write(self._packet(self.CMD_THR, data))

    def send_actuator(self, servo_r: int, servo_l: int,
                      claw_r: int, claw_l: int,
                      cont: int, lights: int,
                      status: int, override: int = 0x88):
        """Send CMD 0x02.  All values are single bytes, clamped to spec.
        override: 0x00=forbid shutdown, 0x88=auto, 0xFF=manual cut."""
        if not self._ser or not self._ser.is_open:
            return
        data = bytes([
            max(0, min(180, servo_r)),
            max(0, min(180, servo_l)),
            max(0, min(200, claw_r)),
            max(0, min(200, claw_l)),
            max(0, min(200, cont)),
            max(0, min(100, lights)),
            status & 0xFF,
            override & 0xFF,
        ])
        with self._lock:
            self._ser.write(self._packet(self.CMD_ACT, data))

    # ── receive (background thread) ──

    def _rx_loop(self):
        while self._running:
            try:
                if self._ser and self._ser.in_waiting:
                    for b in self._ser.read(self._ser.in_waiting):
                        self._feed(b)
                else:
                    time.sleep(0.001)
            except Exception as e:
                print(f"[SERIAL RX] {e}")
                time.sleep(0.1)

    def _feed(self, b: int):
        """Byte-by-byte packet parser — mirrors the Arduino-side parser."""
        s = self._ps
        if s == self.S_START:
            if b == self.START:
                self._csum = b
                self._ps = self.S_CMD
        elif s == self.S_CMD:
            self._cmd = b
            self._csum += b
            self._ps = self.S_LEN
        elif s == self.S_LEN:
            self._dlen = b
            self._csum += b
            if 0 < b <= 32:
                self._buf = bytearray(b)
                self._idx = 0
                self._ps = self.S_DATA
            else:
                self._ps = self.S_START
        elif s == self.S_DATA:
            self._buf[self._idx] = b
            self._idx += 1
            self._csum += b
            if self._idx >= self._dlen:
                self._ps = self.S_CS
        elif s == self.S_CS:
            if (self._csum & 0xFF) == b:
                self._dispatch()
            self._ps = self.S_START

    def _dispatch(self):
        if self._cmd == self.CMD_TEL and self._dlen == 20:
            self._parse_telemetry()

    def _parse_telemetry(self):
        """
        CMD 0x03 — 20-byte payload (little-endian):
          [0-1]   accel X    int16   milli-g
          [2-3]   accel Y    int16   milli-g
          [4-5]   accel Z    int16   milli-g
          [6-7]   gyro  X    int16   deci-°/s
          [8-9]   gyro  Y    int16   deci-°/s
          [10-11] gyro  Z    int16   deci-°/s
          [12-13] depth      uint16  mm
          [14]    throttle % uint8   0–100
          [15]    shutdown   uint8   bitmask
          [16-17] temperature int16  centi-°C
          [18-19] amperage   uint16  milli-A
        """
        ax, ay, az, gx, gy, gz, dmm = struct.unpack_from('<hhhhhhH', self._buf)

        self.st.accel_x = ax / 1000.0
        self.st.accel_y = ay / 1000.0
        self.st.accel_z = az / 1000.0
        self.st.gyro_x = gx / 10.0
        self.st.gyro_y = gy / 10.0
        self.st.gyro_z = gz / 10.0
        self.st.depth = dmm / 1000.0

        self.st.throttle_percent = min(self._buf[14], 100)
        self.st.shutdown_bitmask = self._buf[15]

        temp_centi, = struct.unpack_from('<h', self._buf, 16)
        self.st.temperature = temp_centi / 100.0

        amps_milli, = struct.unpack_from('<H', self._buf, 18)
        self.st.amperage = amps_milli / 1000.0

        az_safe = max(abs(self.st.accel_z), 0.01)
        self.st.pitch = math.degrees(math.atan2(
            self.st.accel_x,
            math.sqrt(self.st.accel_y ** 2 + az_safe ** 2)))
        self.st.roll = math.degrees(math.atan2(
            self.st.accel_y,
            math.sqrt(self.st.accel_x ** 2 + az_safe ** 2)))

        self._last_rx = time.monotonic()

    @property
    def telemetry_age(self) -> float:
        """Seconds since last good telemetry packet (inf if none yet)."""
        if self._last_rx == 0.0:
            return float('inf')
        return time.monotonic() - self._last_rx


# ═══════════════════════════════════════════════════════════════
#  NINTENDO SWITCH PRO CONTROLLER
# ═══════════════════════════════════════════════════════════════

class ControllerInput:
    """Nintendo Switch Pro Controller via pygame — polling + edge detect."""

    A, B, X, Y          = 0, 1, 2, 3
    MINUS, HOME, PLUS   = 4, 5, 6
    LSTICK, RSTICK      = 7, 8
    L, R                = 9, 10
    DUP, DDOWN          = 11, 12
    DLEFT, DRIGHT       = 13, 14
    CAPTURE             = 15

    DEADZONE = 0.12

    def __init__(self):
        self._joy = None
        self.axes = [0.0] * 6
        self._center = [0.0] * 6
        self.buttons = [False] * 16
        self._prev = [False] * 16
        self.connected = False

    def init(self) -> bool:
        if not HAS_PYGAME:
            print("[CTRL] pygame not installed — no controller input")
            return False

        pygame.init()

        count = pygame.joystick.get_count()
        if count == 0:
            print("[CTRL] No controller detected")
            return False

        self._joy = pygame.joystick.Joystick(0)
        self._joy.init()
        self.connected = True
        print(f"[CTRL] {self._joy.get_name()} — "
              f"{self._joy.get_numaxes()} axes, "
              f"{self._joy.get_numbuttons()} buttons")

        time.sleep(0.1)
        self.recalibrate_center()

        return True

    def recalibrate_center(self):
        if not self.connected:
            return
        pygame.event.pump()
        n_axes = min(6, self._joy.get_numaxes())
        self._center = [self._joy.get_axis(i) for i in range(n_axes)]
        while len(self._center) < 6:
            self._center.append(0.0)
        print(f"[CTRL] Center calibrated: "
              f"{[f'{c:+.4f}' for c in self._center]}")

    def poll(self):
        if not self.connected:
            return
        pygame.event.pump()
        self._prev = self.buttons[:]
        for i in range(min(6, self._joy.get_numaxes())):
            v = self._joy.get_axis(i) - self._center[i]
            self.axes[i] = v if abs(v) > self.DEADZONE else 0.0
        for i in range(min(16, self._joy.get_numbuttons())):
            self.buttons[i] = bool(self._joy.get_button(i))

    def pressed(self, btn: int) -> bool:
        return self.buttons[btn] and not self._prev[btn]

    def held(self, btn: int) -> bool:
        return self.buttons[btn]

    @property
    def left_x(self):  return self.axes[0]
    @property
    def left_y(self):  return self.axes[1]
    @property
    def right_x(self): return self.axes[2]
    @property
    def right_y(self): return self.axes[3]

    def shutdown(self):
        if self._joy:
            self._joy.quit()
        if HAS_PYGAME:
            pygame.quit()


# ═══════════════════════════════════════════════════════════════
#  CAMERA MANAGER
# ═══════════════════════════════════════════════════════════════
class CameraManager:

    def __init__(self, ctx: zmq.Context, port: int = 5556):
        self._caps: dict = {}
        self._pub = ctx.socket(zmq.PUB)
        try:
            self._pub.bind(f"tcp://*:{port}")
        except zmq.error.ZMQError:
            print(f"[CAM] Port {port} still held — forcing rebind...")
            self._pub.close()
            self._pub = ctx.socket(zmq.PUB)
            self._pub.setsockopt(zmq.LINGER, 0)
            self._pub.setsockopt(zmq.CONFLATE, 1)
            self._pub.bind(f"tcp://*:{port}")
        self._active: set = set()
        self._running = False
        self._thread: Optional[threading.Thread] = None

    def request_camera(self, idx: int) -> bool:
        if idx in self._caps:
            self._active.add(idx)
            return True
        if not HAS_CV2:
            return False
        cap = cv2.VideoCapture(idx)
        if cap.isOpened():
            self._caps[idx] = cap
            self._active.add(idx)
            return True
        return False

    def release_camera(self, idx: int):
        self._active.discard(idx)
        cap = self._caps.pop(idx, None)
        if cap is not None:
            cap.release()

    def start(self):
        self._running = True
        self._thread = threading.Thread(target=self._loop, daemon=True)
        self._thread.start()

    def stop(self):
        self._running = False
        if self._thread:
            self._thread.join(timeout=2)
        for c in self._caps.values():
            c.release()
        self._caps.clear()

    def _loop(self):
        while self._running:
            for idx in list(self._active):
                cap = self._caps.get(idx)
                if cap and cap.isOpened():
                    ok, frame = cap.read()
                    if ok:
                        _, jpg = cv2.imencode(
                            '.jpg', frame,
                            [cv2.IMWRITE_JPEG_QUALITY, 80])
                        self._pub.send_multipart([
                            f"cam:{idx}".encode(), jpg.tobytes()])
            time.sleep(0.033)
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

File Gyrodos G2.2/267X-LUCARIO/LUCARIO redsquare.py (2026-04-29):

import cv2
import numpy as np

mtx = np.array([[5.74798166e+02, 0.00000000e+00, 1.01247178e+03],
                [0.00000000e+00, 5.83712017e+02, 5.76989155e+02],
                [0.00000000e+00, 0.00000000e+00, 1.00000000e+00]])

dist = np.array([[-0.19427912, 0.03186565, 0.00039767, 0.00129534, -0.0020267]])

SMOOTH = 0.1

# ── Fixed output window size (4:3) ────────────────────────────────────────────
OUTPUT_W = 1024
OUTPUT_H = 768

def undistort_frame(frame, mtx, dist):
    h, w = frame.shape[:2]
    new_camera_mtx, roi = cv2.getOptimalNewCameraMatrix(mtx, dist, (w, h), 1, (w, h))
    undistorted = cv2.undistort(frame, mtx, dist, None, new_camera_mtx)
    x, y, w, h = roi
    undistorted = undistorted[y:y+h, x:x+w]
    return undistorted


def find_red_mask(frame):
    hsv = cv2.cvtColor(frame, cv2.COLOR_BGR2HSV)

    lower_red1 = np.array([0,   40,  40])
    upper_red1 = np.array([10, 255, 255])
    lower_red2 = np.array([160,  40,  40])
    upper_red2 = np.array([180, 255, 255])

    mask = cv2.bitwise_or(
        cv2.inRange(hsv, lower_red1, upper_red1),
        cv2.inRange(hsv, lower_red2, upper_red2)
    )

    kernel = cv2.getStructuringElement(cv2.MORPH_RECT, (5, 5))
    mask = cv2.morphologyEx(mask, cv2.MORPH_OPEN,  kernel, iterations=2)
    mask = cv2.morphologyEx(mask, cv2.MORPH_CLOSE, kernel, iterations=2)
    return mask


def find_square_edges(frame, mask, debug):
    fh, fw = frame.shape[:2]

    diag = np.sqrt(fw**2 + fh**2)
    min_line_len = int(diag * 0.05)
    max_line_gap = int(diag * 0.02)

    edges = cv2.Canny(mask, 50, 150)
    lines = cv2.HoughLinesP(
        edges,
        rho=1,
        theta=np.pi / 180,
        threshold=30,
        minLineLength=min_line_len,
        maxLineGap=max_line_gap
    )

    if lines is None:
        cv2.putText(debug, "No lines found", (20, 40),
                    cv2.FONT_HERSHEY_SIMPLEX, 0.7, (0, 0, 255), 2)
        return None

    horizontals = []
    verticals   = []

    for line in lines:
        x1, y1, x2, y2 = line[0]
        angle = np.degrees(np.arctan2(abs(y2 - y1), abs(x2 - x1)))

        cv2.line(debug, (x1, y1), (x2, y2), (180, 180, 180), 1, cv2.LINE_AA)

        if angle < 20:
            y_mid = (y1 + y2) // 2
            x_s   = min(x1, x2)
            x_e   = max(x1, x2)
            horizontals.append((y_mid, x_s, x_e))
            cv2.line(debug, (x1, y1), (x2, y2), (0, 255, 255), 2, cv2.LINE_AA)

        elif angle > 70:
            x_mid = (x1 + x2) // 2
            y_s   = min(y1, y2)
            y_e   = max(y1, y2)
            verticals.append((x_mid, y_s, y_e))
            cv2.line(debug, (x1, y1), (x2, y2), (255, 0, 255), 2, cv2.LINE_AA)

    def cluster_lines(lines_1d, idx=0):
        if not lines_1d:
            return []
        lines_1d = sorted(lines_1d, key=lambda l: l[idx])
        clusters = []
        current  = [lines_1d[0]]

        for line in lines_1d[1:]:
            if abs(line[idx] - current[-1][idx]) < int(diag * 0.04):
                current.append(line)
            else:
                clusters.append(current)
                current = [line]
        clusters.append(current)

        merged = []
        for cluster in clusters:
            pos   = int(np.mean([l[idx] for l in cluster]))
            start = int(np.min( [l[1]   for l in cluster]))
            end   = int(np.max( [l[2]   for l in cluster]))
            merged.append((pos, start, end))
        return merged

    h_lines = cluster_lines(horizontals, idx=0)
    v_lines = cluster_lines(verticals,   idx=0)

    for (y, xs, xe) in h_lines:
        cv2.line(debug, (xs, y), (xe, y), (0, 255, 0), 2, cv2.LINE_AA)
        cv2.putText(debug, f"H y={y}", (xs, y - 6),
                    cv2.FONT_HERSHEY_SIMPLEX, 0.4, (0, 255, 0), 1)

    for (x, ys, ye) in v_lines:
        cv2.line(debug, (x, ys), (x, ye), (255, 128, 0), 2, cv2.LINE_AA)
        cv2.putText(debug, f"V x={x}", (x + 4, ys + 16),
                    cv2.FONT_HERSHEY_SIMPLEX, 0.4, (255, 128, 0), 1)

    if not h_lines or not v_lines:
        cv2.putText(debug, f"Not enough lines  H={len(h_lines)} V={len(v_lines)}",
                    (20, 40), cv2.FONT_HERSHEY_SIMPLEX, 0.7, (0, 0, 255), 2)
        return None

    y_positions = sorted([l[0] for l in h_lines])
    x_positions = sorted([l[0] for l in v_lines])

    if len(y_positions) >= 2:
        y_top    = y_positions[0]
        y_bottom = y_positions[-1]
    else:
        y_top    = max(0,  y_positions[0] - fw // 4)
        y_bottom = min(fh, y_positions[0] + fw // 4)

    if len(x_positions) >= 2:
        x_left  = x_positions[0]
        x_right = x_positions[-1]
    else:
        x_left  = max(0,  x_positions[0] - fh // 4)
        x_right = min(fw, x_positions[0] + fh // 4)

    cx = (x_left + x_right) // 2
    cy = (y_top  + y_bottom) // 2
    w  = x_right - x_left
    h  = y_bottom - y_top

    # ── Orange bounding box ───────────────────────────────────────────────────
    cv2.rectangle(debug, (x_left, y_top), (x_right, y_bottom), (0, 128, 255), 2)
    cv2.putText(debug, f"cx={cx} cy={cy} w={w} h={h}",
                (x_left, y_top - 10), cv2.FONT_HERSHEY_SIMPLEX, 0.5, (0, 128, 255), 2)

    # ── Shrinking debug boxes ─────────────────────────────────────────────────
    scales = [1.0,          0.90,           0.80,          0.70,          0.60]
    colors = [(200,200,200),(180, 180, 0), (0, 200, 200), (0, 180, 0),  (0, 255, 255)]

    for scale, color in zip(scales, colors):
        bw  = int(w * scale)
        bh  = int(h * scale)
        bx1 = cx - bw // 2
        by1 = cy - bh // 2
        cv2.rectangle(debug, (bx1, by1), (bx1 + bw, by1 + bh), color, 1)

    # ── Actual 4:3 crop box on debug ─────────────────────────────────────────
    crop_w = int(w * 0.80)
    crop_h = int(h * 0.60)
    cx1 = cx - crop_w // 2
    cy1 = cy - crop_h // 2
    cv2.rectangle(debug, (cx1, cy1), (cx1 + crop_w, cy1 + crop_h), (0, 255, 255), 2)
    cv2.putText(debug, "4:3", (cx1 + 4, cy1 + 20),
                cv2.FONT_HERSHEY_SIMPLEX, 0.6, (0, 255, 255), 2)

    return cx, cy, w, h
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

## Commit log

2026-04-11 Rename Gyrodos G2.2/Magikarp Piston adaptor top-z.3mf to Gyrodos G2.2/223X-Gyrodos ROV/26Mec34-Palkia/Magikarp Piston adaptor top-z.3mf
    [Magikarp Piston adaptor top-z.3mf]
2026-04-11 Rename Gyrodos G2.2/Magikarp-Piston adaptor Bottom-Expanded.3mf to Gyrodos G2.2/223X-Gyrodos ROV/26Mec34-Palkia/Magikarp-Piston adaptor Bottom-Expanded.3mf
    [Magikarp-Piston adaptor Bottom-Expanded.3mf]
2026-04-11 Rename Gyrodos G2.2/Palkia - Claw Extension 60.3mf to Gyrodos G2.2/223X-Gyrodos ROV/26Mec34-Palkia/Palkia - Claw Extension 60.3mf
    [Palkia - Claw Extension 60.3mf]
2026-04-11 Rename Gyrodos G2.2/Palkia- Servo Holder-expanded.3mf to Gyrodos G2.2/223X-Gyrodos ROV/26Mec34-Palkia/Palkia- Servo Holder-expanded.3mf
    [Palkia- Servo Holder-expanded.3mf]
2026-04-11 Rename Gyrodos G2.2/Palkia- Stepper Holder R.3mf to Gyrodos G2.2/223X-Gyrodos ROV/26Mec34-Palkia/Palkia- Stepper Holder R.3mf
    [Palkia- Stepper Holder R.3mf]
2026-04-11 Rename Gyrodos G2.2/Palkia-Stepper end loop-expanded.3mf to Gyrodos G2.2/223X-Gyrodos ROV/26Mec34-Palkia/Palkia-Stepper end loop-expanded.3mf
    [Palkia-Stepper end loop-expanded.3mf]
2026-04-11 Rename Gyrodos G2.2/camera clip bottom 180-225.3mf to Gyrodos G2.2/223X-Gyrodos ROV/26Mec34-Palkia/camera clip bottom 180-225.3mf
    [camera clip bottom 180-225.3mf]
2026-04-11 Rename Gyrodos G2.2/stepper holder-485f.3mf to Gyrodos G2.2/223X-Gyrodos ROV/26Mec34-Palkia/stepper holder-485f.3mf
    [stepper holder-485f.3mf]
2026-04-11 Rename Gyrodos G2.2/camera clip bottom 180-45.3mf to Gyrodos G2.2/223X-Gyrodos ROV/26Mec34-Palkia/camera clip bottom 180-45.3mf
    [camera clip bottom 180-45.3mf]
2026-04-11 Rename Gyrodos G2.2/camera clip bottom 180-675.3mf to Gyrodos G2.2/223X-Gyrodos ROV/26Mec34-Palkia/camera clip bottom 180-675.3mf
    [camera clip bottom 180-675.3mf]
2026-04-11 Rename Gyrodos G2.2/camera clip bottom 180-90.3mf to Gyrodos G2.2/223X-Gyrodos ROV/26Mec34-Palkia/camera clip bottom 180-90.3mf
    [camera clip bottom 180-90.3mf]
2026-04-11 Rename Gyrodos G2.2/camera clip top.3mf to Gyrodos G2.2/223X-Gyrodos ROV/26Mec34-Palkia/camera clip top.3mf
    [camera clip top.3mf]
2026-04-11 Rename Gyrodos G2.2/endplate-0-0-8-0-ext16-x.dwg to Gyrodos G2.2/26Mag4X-Magikarp Float/26Mag42-Float Magikarp/endplate-0-0-8-0-ext16-x.dwg
    [endplate-0-0-8-0-ext16-x.dwg]
2026-04-11 Rename Gyrodos G2.2/endplate-10-10-8-71-ext16-y.dwg to Gyrodos G2.2/26Mag4X-Magikarp Float/26Mag42-Float Magikarp/endplate-10-10-8-71-ext16-y.dwg
    [endplate-10-10-8-71-ext16-y.dwg]
2026-04-11 Rename Gyrodos G2.2/endplate-10-13-8-25-ext175-x.dwg to Gyrodos G2.2/26Mag4X-Magikarp Float/26Mag42-Float Magikarp/endplate-10-13-8-25-ext175-x.dwg
    [endplate-10-13-8-25-ext175-x.dwg]
2026-04-11 Rename Gyrodos G2.2/endplate-18-18-8-71-ext16-y.dwg to Gyrodos G2.2/26Mag4X-Magikarp Float/26Mag42-Float Magikarp/endplate-18-18-8-71-ext16-y.dwg
    [endplate-18-18-8-71-ext16-y.dwg]
2026-04-11 Rename Magikarp Piston adaptor top-z.3mf to Magikarp Piston adaptor top-z.3mf
    [Magikarp Piston adaptor top-z.3mf]
2026-04-11 Rename Magikarp-Piston adaptor Bottom-Expanded.3mf to Magikarp-Piston adaptor Bottom-Expanded.3mf
    [Magikarp-Piston adaptor Bottom-Expanded.3mf]
2026-04-11 Add gitkeep file for 261X Gyrodos Crab Detection
2026-04-11 Rename Magikarp Piston adaptor top-z.3mf to Magikarp PAWMO.3mf
    [Magikarp PAWMO.3mf]
2026-04-11 Fix links in README for LUCARIO and CAD files
    Updated links in README to point to the correct GitHub repository paths.

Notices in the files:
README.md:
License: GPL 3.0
